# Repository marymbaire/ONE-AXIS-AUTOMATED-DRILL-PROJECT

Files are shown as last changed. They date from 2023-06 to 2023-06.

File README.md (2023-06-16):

# ONE AXIS AUTOMATED DRILL PROJECT
 All files regarding project will be saved here
Follow this link to install github desktop and clone the repository: https://youtu.be/xuq73UJrbwg
To add your files to github, create a branch and commit changes(add your files) to your branch, the owner( Mary) will merge changes to the main branch. Follow this link to create branch and commit changes to branch: https://youtu.be/Lf3DYRvCPFo. Your created branch should now be accessible on github desktop. Always push changes to your branch(not Main).

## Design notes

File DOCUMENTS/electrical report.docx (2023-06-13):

Electrical design

The design for the electrical circuit and simulation was done on Proteus because it was user friendly and suited our project needs.

Achievements

- Successfully controlled the feed rates and cutting speeds using feedbacks from the vibration, force and temperature sensor.
- Able to monitor the input and output parameters in real time using a Virtual Serial Monitor.
- Programmed our Arduino UNO microcontroller on Arduino software which would then control our process.

Challenges

- The virtual monitor delayed to display the data on the start of the simulation as the input parameters were altered.
- Running the stepper motor at higher speeds results to the motor wobbling.

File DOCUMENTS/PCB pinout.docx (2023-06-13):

| Signal pin | Power pin
Stepper | B7(pul),A8(dir) | N/a
L298N dc motor control | B12(EN),B13(IN1),B14(IN2) | N/A
Vibration sensor 1 | A5 | Pwr + gnd
Vibration sensor 2 | 10 | Pwr + gnd
Limit switch | A11 | Pwr + gnd
Encoder | B0, B1 | Pwr + gnd
Temperature sensor | B8, B9
Load cell | B4, B5
start | A3 | PWR
Stop | A1
Bluetooth module | B6, B7, B3 | Pwr + gnd
Start LED | A15
Stop LED

VIB+TEMP+LOAD = PWR+GND

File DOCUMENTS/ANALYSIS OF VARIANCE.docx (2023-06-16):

ANALYSIS OF VARIANCE(ANOVA)

1. Data collection

The goal of this analysis is to obtain optimal operating points for the stepper motor which provides linear feed to the dc motor station and the dc motor speed which provides rotary feed to the workpiece.

The two hypotheses in the experiment:

Null hypothesis: There is no significant difference in the mean quality of drilling across different levels of linear feed speed provided by the stepper motor and rotary speed determined by the DC motor.

Alternative hypothesis: There is a significant difference in the mean quality of drilling across different levels of linear feed speed provided by the stepper motor and rotary speed determined by the DC motor.

| Stepper Motor Speed (RPM) | DC Motor Speed (RPM) | Drill performance
E0 | 26.7 | 7958 | 0
E1 | 30.0 | 9422 | 0
E2 | 24.2 | 9422 | 0
E3 | 17.4 | 9604 | 3
E4 | 17.8 | 9775 | 3
E5 | 17.4 | 9712 | 2
E6 | 9.8 | 9778 | 8
E7 | 9.9 | 9671 | 5
E8 | 9.4 | 9733 | 8
E9 | 31.1 | 9785 | 5
E10 | 21.4 | 9836 | 5
E11 | 4.5 | 9706 | 3

2. ANOVA analysis

Drill performance extremes: 0- does not drill

10- drills efficiently

ANOVA: Two-Factor Without Replication
SUMMARY | Count | Sum | Average | Variance
E0 | 2 | 7984.7 | 3992.35 | 31452760
E1 | 2 | 9452 | 4726 | 44104832
E2 | 2 | 9446.2 | 4723.1 | 44159322
E3 | 2 | 9621.4 | 4810.7 | 45951450
E4 | 2 | 9792.8 | 4896.4 | 47601476
E5 | 2 | 9729.4 | 4864.7 | 46992635
E6 | 2 | 9787.8 | 4893.9 | 47708866
E7 | 2 | 9680.9 | 4840.45 | 46668427
E8 | 2 | 9742.4 | 4871.2 | 47274198
E9 | 2 | 9816.1 | 4908.05 | 47569283
E10 | 2 | 9857.4 | 4928.7 | 48163187
E11 | 2 | 9710.5 | 4855.25 | 47059551
Stepper Motor Speed (RPM) | 12 | 219.6 | 18.3 | 75.45818
DC Motor Speed (RPM) | 12 | 114402 | 9533.5 | 264111
ANOVA
Source of Variation | SS | df | MS | F | P-value | F crit
Stepper*DC Motor | 1434252 | 11 | 130386.5 | 0.974489 | 0.516708 | 2.81793
Stepper and DC Motor Separately | 5.43E+08 | 1 | 5.43E+08 | 4060.048 | 1.76E-15 | 4.844336
Error | 1471799 | 11 | 133799.9
Total | 5.46E+08 | 23
Total | 7.28E+08 | 35

3. Interpretation of ANOVA results
- The p-values indicate the significance of each factor and their interactions.
- Stepper Motor Speed has a p-value of <0.05, indicating that it has a significant effect on Optimal Drilling Performance.
- Drill Motor Speed also has a p-value of <0.05, suggesting a significant effect on Optimal Drilling Performance.
- Both the stepper motor speed and the drill motor speed independently significantly impact the quality or efficiency of the drilling process for PMMA material.
- The interaction between Stepper Motor Speed and Drill Motor Speed has a p-value of 0.516708, which is not statistically significant. Therefore, the interaction does not have a significant effect on Optimal Drilling Performance.
- The p- value of interaction between stepper motor speed and dc motor speed is greater than 0.5, thus we fail to reject null hypothesis; this means there is no significant difference in the mean quality of drilling across different levels of linear feed speed provided by the stepper motor and rotary speed determined by the DC motor. This means that the two variables can be controlled independent of each other to obtain best quality drilling.

From the analysis, the number of times the station is able to carry out a successful drilling operation is limited. The station exhibits a successful drilling operation when a starting hole is provided. Failure to drill can be attributed to the melting of PMMA and the sticking of the melted PMMA on the drill bit, making further drilling difficult. The new PMMA used melts when heated during heating. Using the current setup as it is, the optimal operating parameters is at 200 pulses/rev setting for stepper motor, where it operates at 21.6 rpm and for the dc motor, at 255PWM, which is equivalent to 9778rpm, which can be conditioned separately, with one of the variables held constant.

Recommendations

Using a geared dc motor for the drill station with operating speed limit of 300 rpm will provide sufficient torque to drill the PMMA as it melts. Temperature should also be control variable in the system due to thermal behavior of the PMMA strip.

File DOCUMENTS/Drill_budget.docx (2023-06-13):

ITEM | ADDRESS | UNITS | COST | TOTAL COST
Nema 17 Stepper motor | Nema 17 Stepper motor, 12V 0.4A, 1.8 degree, 2 phase 6 wires | ATO.com (https://www.ato.com/nema-17-stepper-motor-12v-0-4a-1-8-degree-2-phase-6-wires) | 1 | 6585/= | 6585/=
MLX90614ESF Non-contact Infrared Temperature Sensor Module (https://www.amazon.com/gp/slredirect/picassoRedirect.html?id=2962699365333126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) | Amazon.com : MLX90614 (https://www.amazon.com/MLX90614/s?k=MLX90614) | 1 | 1779/= | 1779/=
801S Vibration Sensor Module | 801S Vibration Sensor Module - ProtoSupplies (https://protosupplies.com/product/801s-vibration-sensor-module/) | 2 | 450/= | 900
HX711 LOAD CELL AMPLIFIER+5Kg | HX711 LOAD CELL AMPLIFIER+5Kg – Besomi Electronics (besomi-egypt.com) (https://besomi-egypt.com/products/hx711-load-cell-amplifier-5kg) | 1 | 2,310.27 | 2310.27
TB6600 DC 4A 9-42V Stepper Motor Driver | Generic TB6600 DC 4A 9-42V Stepper Motor Driver CNC @ Best Price Online | Jumia Kenya (https://www.jumia.co.ke/generic-tb6600-dc-4a-9-42v-stepper-motor-driver-cnc-61027590.html) | 1 | 5,395 | 5,395
L298N MOTOR DRIVER | Shop & Buy Online | Jumia Kenya (https://www.jumia.co.ke/catalog/?q=L298N+MOTO) | 1 | 1897 | 1897
12V DC MOTOR with drill chuck | Shop & Buy Online | Jumia Kenya (https://www.jumia.co.ke/catalog/?q=dc%20motor+chuck) | 1 | 300 | 2200
12v dc power supply | Shop & Buy Online | Jumia Kenya (https://www.jumia.co.ke/catalog/?q=12v+dc+power+supply) | | 3800 | 4000
total | | | | 25066

Automatic drill project budget

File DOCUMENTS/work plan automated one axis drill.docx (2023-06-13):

ONE AXIS AUTOMATED DRILL 10 WEEK WORK PLAN FOR OCTOBER- FEBRUARY SEMESTER

WEEK NUMBER | DATES | ACTIVITY | OBJECTIVE | INVOLLVEMENT
1. | 7th November- 13th November | In depth familiarization with existing model | - Analysis of mechanical set- up, identifying improvement areas. - Analysis of circuitry, identifying improvement areas - Analysis of used code and MATLAB files | 3 meetings during the week of all group members at the drill station (Monday, Wednesday, Friday)
2. | 14th November- 20th November | Full model design in SolidWorks | To design the full setup of the physical model with the improvements made. | Division of parts among group members, each tackling own design part, meetings to analyze progress and assemble, 2 group meetings.
3. | 21st November- 27th November | Importing CAD Files to MATLAB and modelling | Simulate the mechanical set-up in MATLAB | All group members involved. 3 meetings during the week.
4. | 28th November- 4th December | Finite element analysis in Abaqus | Analysis of forces of the system | All group members involved. 3 meetings during the week.
5. | 5th December- 11th December | Finite element analysis in Ansys | Analysis of forces of the system | All group members involved. 3 meetings during the week.
6 and 7 | 12th December- 23rd December | Circuit design in Proteus | Full circuit design of system | All group members involved. 2 meetings per week, total 4 meetings.
8 and 9 | 2nd January- 13th January | Programming of system and simulation | Development of embedded program. | All group members involved. 2 meetings per week.
10 | 14th January- 18th January | Analysis of objectives and challenges | | All group members involved. 2 meetings in the week.

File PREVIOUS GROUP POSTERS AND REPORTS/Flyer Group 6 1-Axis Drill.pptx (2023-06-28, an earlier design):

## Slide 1

Group members
1. Calvin Shibiriti.
2. Silvester Momanyi.
3. Allan Waithira.
4. Brilliant Chepkirui.
5. Joseph Kiarie.

OVERVIEW

STUDY AND DEVELOPMENT OF
AN AUTOMATED
1-AXIS DRILL

PROBLEM STATEMENT
Common problems in drilling include chatter vibrations, drill bit breakage, and work piece damage. This study seeks to use data from force, vibration, and temperature sensors to minimize chatter, and obtain quality cuts without increasing throughput time. Perspex was chosen for study since it resembles the human bone in properties.

OBJECTIVES
- Condition monitoring when drilling.
- Control the operation using STM32 Blue Pill.
- Conduct and validate Finite Element Analysis on Abaqus.

September 2022

Supervisor: Dr. Titus Mulembo

INTRODUCTION
Today’s market has simple drilling machines and often, human operator is required to drill the hole. Accuracy cannot be attained properly due to high temperatures which may spoil the job due to human errors. To overcome all these problems, this automated drilling machine is designed which is aimed to drill the holes automatically over a job according to the drilling depth data programmed through a key board.

JUSTIFICATION
There has been an increasing demand for acrylic materials such as PMMA, owing to their mechanical and thermal properties. In the medical industry, the drilling of bone is a common procedure in orthopaedic surgery to produce holes for screw insertion to fixate the fracture devices and implants. PMMA is compatible with the human bone which has promoted its use in orthopedic research.

EXPERIMENTAL WORK

Determination of drilling control parameters
Upload the program to the microcontroller
Run the experiment
Results and Data Collection
Evaluation and analysis

Sample Sensor Data

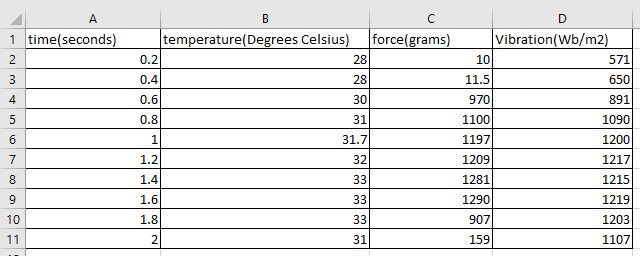
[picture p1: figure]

Fabricated Drill Set Up

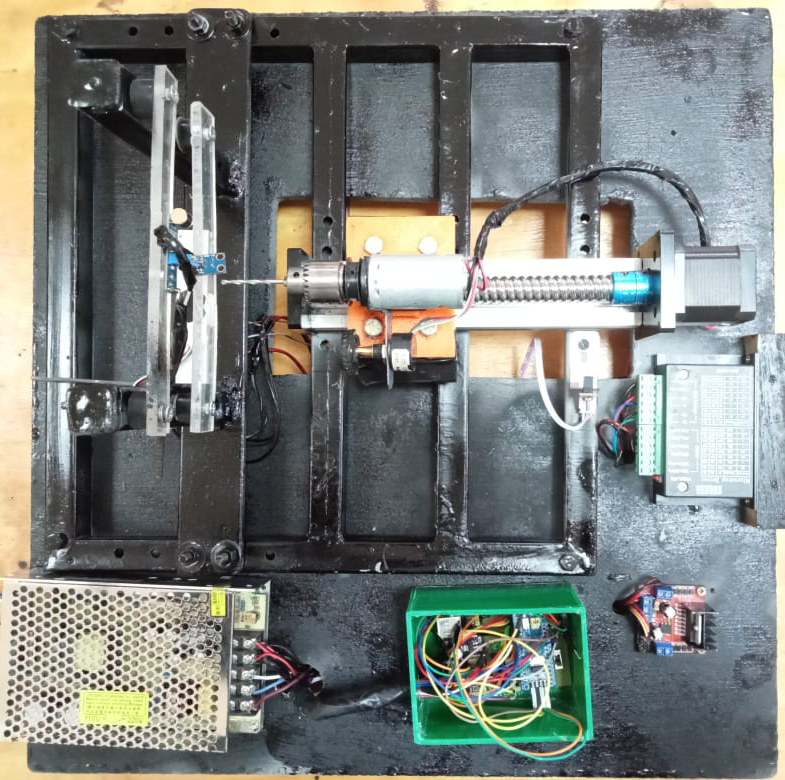
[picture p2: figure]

VARIABLES

- Feed rate
- Spindle speed
- Drill bit diameter
- Hole Depth

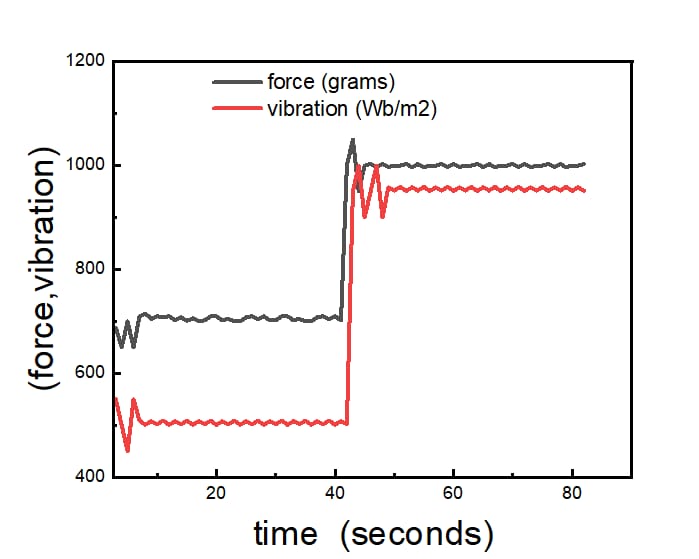
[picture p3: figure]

Graph of vibration (Wb/m²) against time (seconds)

RESULTS

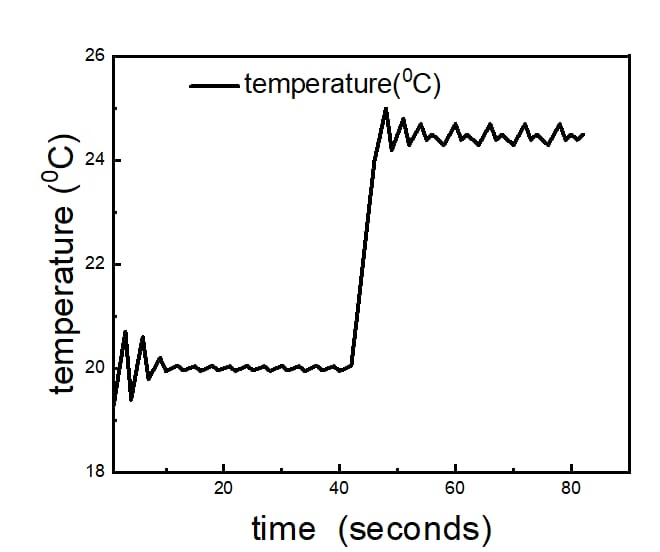
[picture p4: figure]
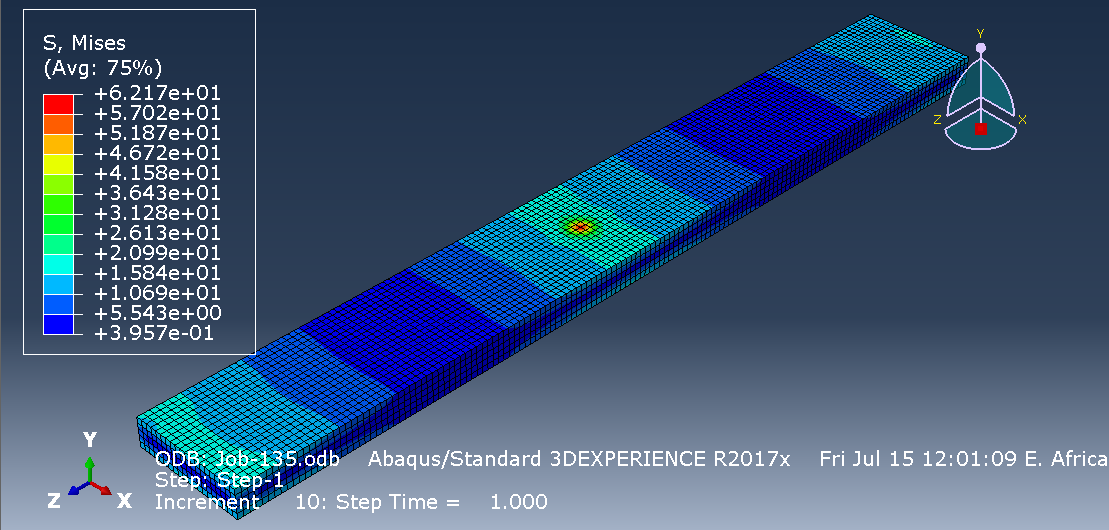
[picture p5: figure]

Analysis of PMMA when subjected to a load

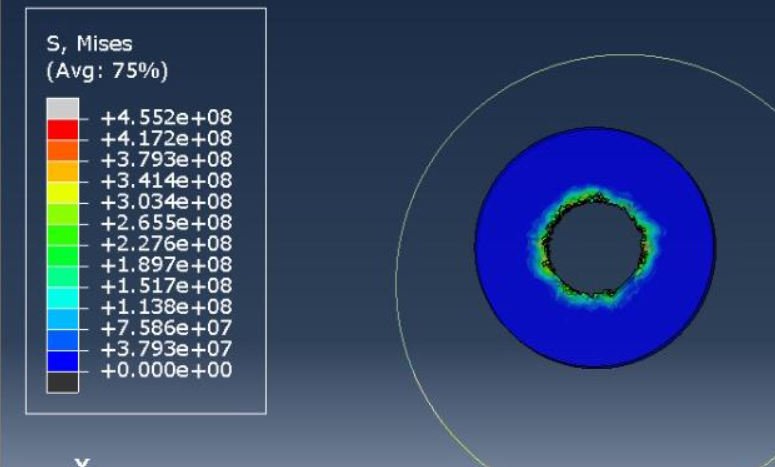
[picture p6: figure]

Temperature evolution upon drilling

- The condition of the drilling action was monitored using the three sensors; temperature, force, and vibration sensors.
- Data was collected and transmitted to an external computer module via Bluetooth.
- The data was simulated and analyzed using Matlab.

Graph of Temperature (Degrees Celsius) against Time (seconds)

CONCLUSION

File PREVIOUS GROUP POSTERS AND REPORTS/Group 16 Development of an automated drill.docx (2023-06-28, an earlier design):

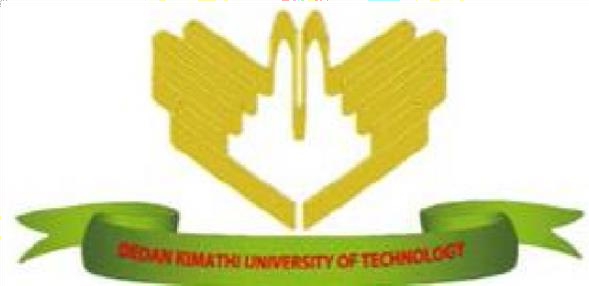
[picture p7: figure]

DEDAN KIMATHI UNIVERSITY OF TECHNOLOGY

SCHOOL OF ENGINEERING

DEPARTMENT OF MECHATRONICS ENGINEERING

1. ONYUNA AGGREY OMONDI E022-01-0747/2017
2. NAFULA FAITH E022-01-0749/2017
3. ADEGU GLORIA VUHYA E022-01-0737/2017
4. ISAAC MWONDI VENANT E022-01-0726/2017

TITLE: STUDY AND DEVELOPMENT OF AN AUTOMATED DRILL

A project proposal submitted in partial fulfillment of the requirement for the award of the Degree of Bachelor of science in Mechatronic Engineering in the Dedan Kimathi University of Technology.

FEBRUARY 2022

# ACKNOWLEDGEMENT

We would like to thank the almighty God for gift of life and good health during the preparation of this research undertaking. Our heartfelt gratitude also goes to our able supervisor Dr. Titus Mulembo, who we have worked closely with in preparation and undertaking of this research. We also wish to acknowledge the entire Department of Mechatronic Engineering of Dedan Kimathi University of Technology for the support they have given us during this process. To our colleagues, friends and parents who gave us support in any manner, we are grateful indeed.

ABSTRACT

Acrylic polymers and co-polymers are currently widely used in industry in all kinds of applications due to their chemical purity, stability, high heat resistance, sunlight resistance, excellent weathering, low-temperature performance, water resistance, and hydrophobicity. Acrylic is very scratch resistant compared to other transparent plastics. It is a lighter alternative to glass and an

economical substitute for polycarbonate in applications where strength is not crucial.

Due to its wide applications, various manufacturing processes are performed on acrylic, drilling one of them. Drilled holes can be produced on the acrylic using conventional or non-conventional drilling processes. Conventional micro-drilling uses drill bits of different configurations such as twist, spade, D-shaped, single flute, compound drill, and coated micro drill. In contrast, non-conventional micro-drilling involves electrical, chemical, mechanical, and thermal means, including laser, EDM, ECM, SACE, electron beam, ultrasonic vibration, or combinations of these approaches.

Various researchers and manufacturing companies working with PMMA have proposed different guidelines for drilling PMMA. The spindle speed, feed rate, tool point angle, coolant & lubricating agent, vibration, tool material, clearance, and chip length influences the drilling process. These machining parameters must be optimized in order to produce quality holes and maintain the material properties of the machined workpiece for long service life

The current work focuses on developing an automated drilling machine that measures the drilling parameters required for drilling different hole sizes on PMMA.

© 2017 The Authors. Published by Elsevier B.V.

Peer-review under responsibility of the scientific committee of The 50th CIRP Conference on Manufacturing Systems.

## 1. INTRODUCTION

PROBLEM STATEMENT

Current automatic CNC machines used to drill PMMA are expensive. In addition, the alternatives used, such as the hand drill, are frequently marred by drill bit breakage, mainly inexperienced users. On the other hand, if the workpiece or drill-bit is not tightly held, walking phenomena occur where the drill bit tends to skid away from the desired drilling coordinates giving a significant blow to the precision of drilled holes.

There is a need to develop an inexpensive automated drilling machine that addresses all these challenges. In contrast with the available CNC drilling machines, the proposed automated drill has the advantages of lower cost, less construction difficulty, and maintenance that is more convenient. It is also a more straightforward use; hence, it produces quality and curbing bit breakage for thin drill bits and drill bit wear for thick drill bits.

JUSTIFICATION

Currently, the drilling of PMMA is by using automatic CNC machines. However, this method has proved to be expensive, and its availability to the ordinary person is limited.

The other alternative used is the hand drill frequently marred by the drill bit breakage, primarily inexperienced users. On the other hand, if the workpiece or drill bit is not tightly held, a walking phenomenon occurs where the drill bit tends to skid away from the desired drilling coordinates giving a significant blow to the precision of the drilled holes.

The automated drill finds it suitable for PMMA drilling because it is less expensive. Therefore, it saves on costs has high accuracy and precision. In addition, this production of quality drill holes and the machining parameters are continuously monitored and optimized for the entirety of the drilling process, thus saving time.

In contrast with the available CNC drilling machines, the proposed automated drill will have the advantages of lower costs, less construction difficulty, more convenient maintenance, and simpler to use, hence producing quality and curbing bit breakage for thin drill bit wear for thick drill bits.

In the recent past, we have seen a tremendous rise in the use and application of acrylic polymers. From the aerospace industry to the entertainment industry, PMMA is being used for various purposes, leading to various manufacturing processes, including drilling.

The automated drill finds its suitability in PMMA drilling because it is less expensive has high accuracy and precision. The machining parameters are automatically monitored and optimized for the entirety of the drilling process. In addition, the machine uses the peck cycle drilling, where the workpiece is drilled intermittently, for adequacy.

## OBJECTIVES.

### Main Objective.

To design and fabricate an automated drilling machine for PMMA drilling.

Specific Objectives

## i. To design and fabricate an automated drilling machine.

## ii. To design mechanical assembly simulations using CAD software.

## iii. To design an electrical circuit that interfaces with the sensors during the drilling operation.

## iv. To monitor force, thermal fluctuations, and optical characterization

## v. To enable drilling of quality, thin/long holes.

## vi. To design optimal machining conditions for drilling of PMMA (polymethyl methacrylate).

## PROJECT SCOPE

As outlined above, our project will mainly focus on designing and fabricating an automated drill that ensures drilling of quality thin, long holes while monitoring parameters such as temperature and vibrations to determine optimum drilling parameters.

2. METHODS

In order to achieve quality drilling of holes using optimum conditions such as the feed rate, drilling speed, and drill bit diameter, we had to follow the required steps as follows:

a) Coming up with CAD Models and electrical circuits using softwares: achieved through Solidworks, Proteus, Fritzing
b) Simulations of the whole system and its components using Simscape, Proteus, Abaqus: Simulations that show how the system would move prior to fabrication, temperature and force simulations of the workpiece and simulations of the electric components too.
c) Actual fabrication of the rig: Assembly of all the mechanical parts. Processes included welding, woodcutting, bolting, painting
d) Circuit interfacing of the sensors, actuators and drivers and their programming:
e) Running the experiments and data collection and observation to determine the optimum parameters: Running the motors sequentially to approach the workpiece, drill the PMMA while sensors are collecting data then move back to the original position.

Experimental Rig

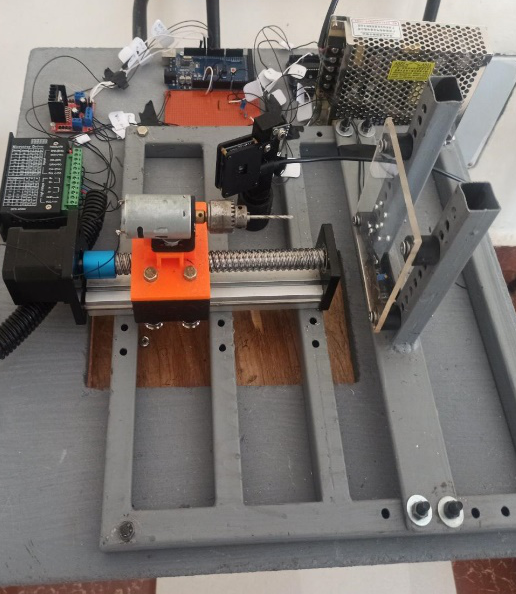
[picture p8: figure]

Figure 1: an image of the whole assembly

Components

- NEMA 17 Stepper motor.
- DC Motor.
- 801S Vibration sensor module.
- MLX0614 non-contact Infrared temperature sensor.
- TB6600 Microstep stepper motor driver.
- L298N DC motor driver.
- Arduino Mega

Procedure

This involved drilling with drill bits of different diameters while varying their feed rates until the optimum parameters were identified.

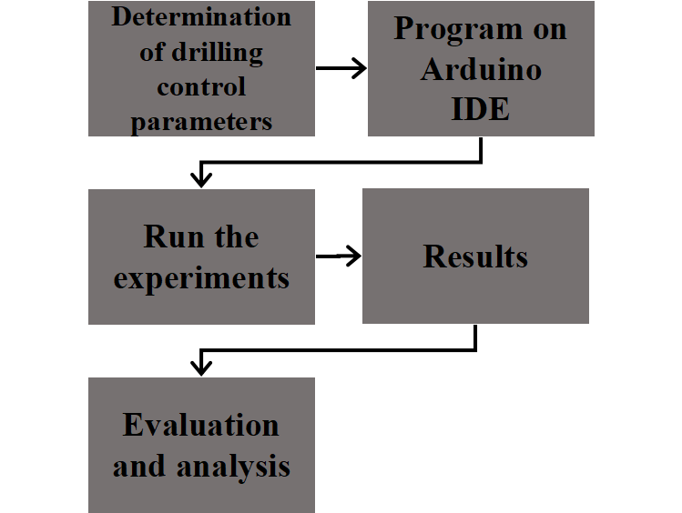
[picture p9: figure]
FLOW CHART

3. EXPERIMENTAL RESULTS

Temperature from MLX90614

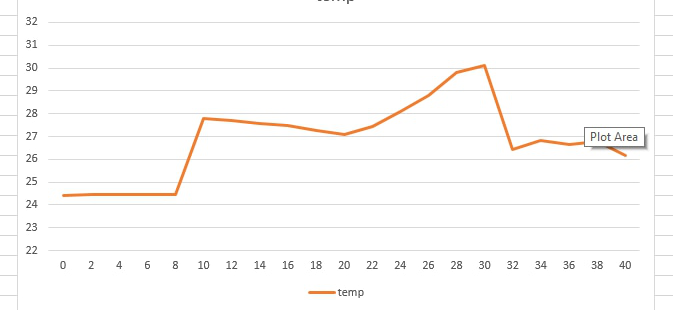
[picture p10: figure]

Figure 2: A graph of temperature from MLX90614 temp sensor

Temperature from ABAQUS simulation

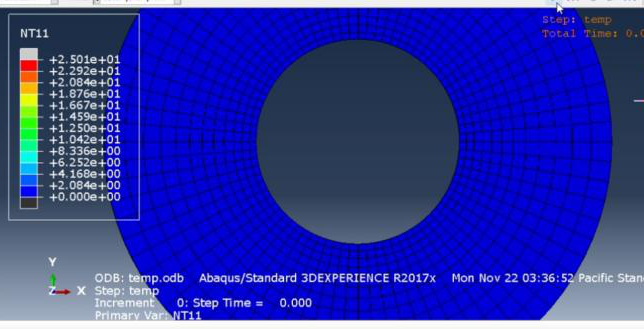
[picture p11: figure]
WhatsApp Image 2022-02-16 at 12.07.23

Figure 3: An Image of the temperature simulation using Abaqus before the drilling process starts

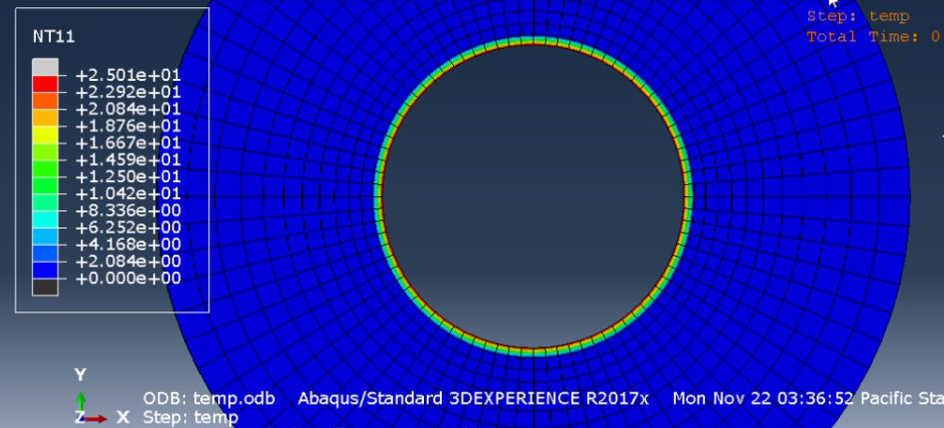
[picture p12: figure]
WhatsApp Image 2022-02-16 at 12.07.26

Figure 4: An image of the workpiece in Abaqus temperature simulation during the drilling process

Expected Vibration output from 801S Vibration sensor

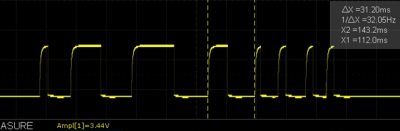
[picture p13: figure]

Figure 5: 801S Vibration sensor expected output

Its output switches shortly from LOW to HIGH depending on the vibrations during the drilling process. A threshold value was set on the onboard potentiometer where drilling was safe.

Hole Quality

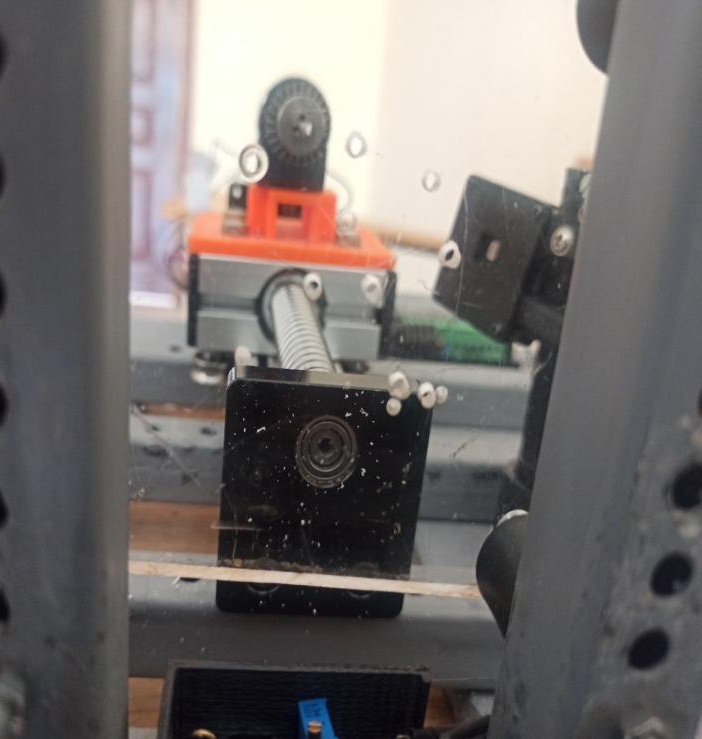
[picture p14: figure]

Figure 6: An Image of the PMMA Workpiece showing different holes

4. DISCUSSION

The drilling speeds were achieved with (Pulse Width Modulation) PWM by the Arduino Mega 2560. The motor had a maximum (Revolutions per Minute) RPM of 12000, which in turn, correlated which a maximum setting of 255 on PWM. We used different RPM according to the drill bit diameter in order to ensure we achieved quality holes.

We also had another parameter to control which was the feed rate (mm/rev). This is the velocity at which the cutter is advanced against the workpiece. This was being controlled by the stepper motor.

The following are the drilling parameters that were achieved to produce quality holes on the PMMA sheet.

During the drilling process, we were monitoring vibrations and temperature to ensure optimal parameters that would lead to quality holes. The temperature was being monitored by the MLX 90614 temperature sensor while the vibrations were being monitored by the 801S vibration sensor.

Temperature from Abaqus simulations matched with the actual results from the experiment as predicted.

5. CONCLUSIONS
- The automated drill was able to drill as expected, and the parameters for optimum drilling were determined for production of quality holes.
- Temperature and vibration were able to be monitored during the drilling process.
- The vibration signals are considered to contain reliable features for monitoring drill wear and breakage.
- It is also time effective, inexpensive and easy to use.

RECOMMENDATIONS

We would recommend that if the project is to be improved, there should be:

- An introduction to feedback control
- Making the project smart such as use of a Bluetooth module to operate it from a remote position.
- Introducing another axis.

REFERENCES

1) Brandrup J, Immergut EH, Grulke EA, editors. Polymer Handbook. 4th ed. New York: John Wiley & Sons; 1999
2) Ulrich H. Introduction to Industrial Polymers. Munich: Hanser; 1982
3) Rey-Vinolas S, Engel E, Mateos- Timoneda MA. Polymers for bone repair. In: Bone Repair Biomaterials. Woodhead Publishing Series in Biomaterials. UK: an imprint of Elsevier; 2019. pp. 179-197. DOI: 10.1016/ b978-0-08-102451-5.00007-x
4) Modelling and optimization of temperature in orthopaedic drilling: An in vitro study RUPESH KUMAR PANDEY, SUDHANSHU SEKHAR PANDA
5) https://www.researchgate.net/publication/232167295_Finite-Element_Analysis_of_Forces_in_Drilling_of_Ti-Alloys_at_Elevated_Temperature
6) Finite Element Analysis of Drilling Frame on Down-the-Hole Drill Based on Mechanical Mechanics and Mechanical Properties | Scientific.Net : https://www.scientific.net/AMR.908.282
7) (PDF) 3D Finite Element Modelling of Drilling Process: https://www.researchgate.net/publication/317271692_FEM_Simulation_of_Tool_Wear_in_Drilling

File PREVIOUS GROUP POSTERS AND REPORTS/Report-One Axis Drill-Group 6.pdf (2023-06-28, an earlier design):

### P a g e | 1

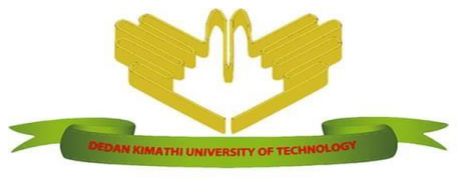
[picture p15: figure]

DEDAN KIMATHI UNIVERSITY OF TECHNOLOGY

MECHATRONIC DEPARTMENT – SCHOOL OF ENGINEERING

1. SHIBIRIT CALVINE | E022-01-1056/2018
2. OMWAGA SILVESTER | E022-01-1412/2018
3. WAITHIRA ALLAN | E022-01-0496/2018
4. CHEPKIRUI BRILLIANT | E022-01-1053/2018
5. KIARIE JOSEPH | E022-01-1085/2018

TITLE: STUDY AND DEVELOPMENT OF AN AUTOMATED DRILL

STUDENTS` REPORT

Submitted in September 2022

A report submitted in partial fulfilment of the requirements for the award of a degree in

Mechatronic Engineering.

### Department of Mechatronic Engineering

ABSTRACT

There are broad applications of high aspect

ratios, high quality holes. However, it is very

difficult for conventional drilling methods to

obtain deep holes, especially with high aspect

ratio, while keeping vibrations, forces, and

thermal evolution on check. This automated 1-

axis drill provide a promising solution for

efficient drilling of deep holes with high-

precision material removal, reduced cracks or

breakage of workpiece, minimized heat-affected

zones. Monitoring the system is crucial in

determining optimal drilling parameter which

can in turn be used in a system control. On the

same note, this research analyzes the behavior

of PMMA during the drilling action. Finally,

the analysis of the material composition could

help other students or researchers in studying

plastics behaviour to heat and stress.

Key Words: Automatic 1-Axis Drill,

PMMA, force, vibrations, temperature

### 1. Introduction

Drilling is a cutting process that uses a drill

bit to cut a hole of circular cross-section in solid

materials. Recently, drilling of quality holes in

Perspex has gained a lot of research interest

especially in thermoplastics and human bones.

This study attempts to contribute to this

endeavor by proposing to design and fabricate a

1-axis automated drilling machine that will

monitor key conditions of the system during operation. To achieve quality drilling, the

effects of three sensors will be studied for:

drilling | force, | vibration, | and | cutting
temperatures | monitoring. | The | automated

drilling machine and its electronics are designed

in CAD and simulated in Matlab. Temperature

evolution and stresses on the Perspex are

studied using FEA. The collected data in a live

feed and simulations done for analysis.

Mechanical transmission is done with a stepper

motor based on the drilling depth fed into the

program. | The | entire | process | utilizes

mechatronics and various related fields in order

to fulfil the drilling objective.

### 1.1 Problem Statement

Common problems in drilling include chatter

vibrations, drill bit breakage, and workpiece

damage. This can present challenges in

precision drilling applications in the delicate

technological drilling and medical industry.

This study seeks to use data from force,

vibration, and temperature sensors to minimize

chatter, and obtain quality cuts without

increasing throughput time. Perspex was

chosen for study since it resembles the human

bone properties.

### 1.2 Justification

In the medical industry, the drilling of bone is a

common procedure in orthopedic surgery to

produce holes for screw insertion to fixate the

fracture devices and implants. It also helps with

fix plates and screws that fastens broken body

parts for immobilization. In the recent past,

bone drilling has gained popularity following its importance in reduction of tissue damage, a

process known as osteonecrosis. PMMA has

similar properties to the bone hence this study

can be used in orthopedic drilling research.

### 2. OBJECTIVES

2.1 Main Objective

To design and create a 1-axis automatic drilling

machine with a monitoring system of the

drilling parameters.

2.2 Other Objectives

- To design mechanical
assembly simulations using CAD.
- To program the sensos and actuators for the operation using STM32 Blue Pill.
- To monitor the drilling
operation in MATLAB.
- To conduct a Finite Element Analysis on Abaqus.

### 2.3 Project Scope

Interfacing of all software necessary for the

design of the automated one axis drilling

machine are bound within the scope of this

project. In addition, assembling of the hardware

components and whole design architecture also

falls under the scope of the project. Finally,

some of the properties deemed important and

worth evaluating from this project include its

efficiency and reliability. Designing of the

proposed automated one axis drilling machine

is covered in the scope of this project.

3. METHOD

### 3.1 Steps

In order to achieve quality drilling of holes

using optimum conditions such as the feed

rate, drilling speed, and drill bit diameter,

we had to follow the required steps as

follows:

a) Coming up with CAD Models and electrical

circuits using software: achieved through

Solidworks, Proteus, Fritzing.

b) Simulations of the whole system and its
components | using | Simscape, | Proteus,

Abaqus and Solidworks:

- Simulations that show how the system would

move prior to fabrication,

i. temperature and force simulations of the

work piece

ii. Simulations of the electric components.

iii. Mechanical design simulation.

c) Actual fabrication of the rig:
- 3D printing of components such us:
i. pulleys,

ii. electrical cabinet.

- Assembly of all the mechanical parts.

Processes included:

i. welding,

ii. bolting,

iii. painting

d) Circuit interfacing of the sensors, actuators

and drivers and their programming:

e) PCB fabrication.
f) Running the experiments and data collection

and observation to determine the optimum

parameters: Running the motors sequentially

to approach the workpiece, drill the PMMA

while sensors are collecting data then move

back to the original position.

g) Interfacing the digital twin of model.

### 3.2 Components

- NEMA 17 Stepper motor.
- DC Motor.
- 801S Vibration sensor module.
- MLX0614 | non-contact | Infrared

temperature sensor.

- TB6600 Micro-step stepper motor

driver.

- L298N DC motor driver.
- STM32 Blue Pill microcontroller.
- Speed Encoder
- Photoelectric Limit Switch
- Ball screw

### 3.3 PROCEDURE

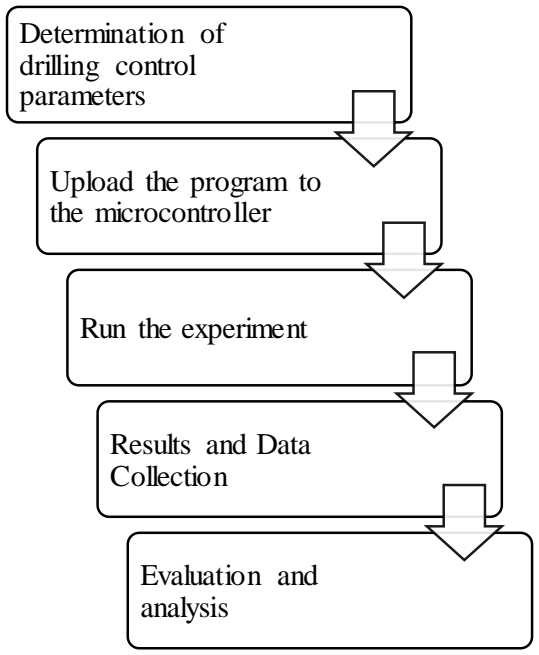
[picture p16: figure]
Determination of drilling control parameters; Upload the program to the microcontroller; Run the experiment; Results and Data Collection; Evaluation and analysis

### 3.4 Components

Stepper Motor

One of the main electrical components used

in this project is the stepper motor. It

contains the carriage that holds the DC motor

in | position.

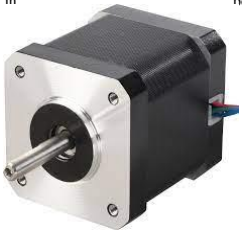
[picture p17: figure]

Figure 1: A stepper motor

In a stepper motor, the electromagnets are

energized by an external control circuit, such

as a microcontroller. To make the motor

shaft turn, first one electromagnet is given

power, which makes the gear's teeth

magnetically attracted to the electromagnet's

teeth. When the gear's teeth are thus aligned

to the first electromagnet, they are slightly

offset from the next electromagnet. So, when

the next electromagnet is turned on and the

first is turned off, the gear rotates slightly to

align with the next one, and from there the

process is repeated. Each of those slight

rotations is called a "step," with an integer

number of steps making a full rotation. In

that way, the motor can be turned by a

precise angle. Stepper motors are ideally

suited for precise positioning of an object or

precise control of speed without having to

resort to closed loop feedback. These motors

rotate in step-wise i.e., this stepper motor

rotates a precise angular distance, one step

for each pulse that is delivered to its drive circuit. The motor used in this project work

has a step angle of 1.80 per pulse. In order to

rotate the motor shaft for one complete

revolution i.e., 3600, it is required to supply

200 pulses (360 / 1.80 = 200) to the motor’s

drive circuit. This drive circuit is then

connected to drilling machine, which is the

main device of the project.

STM 32 Blue Pill

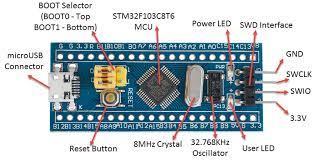
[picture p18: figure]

Figure 2: STM 32 Blue Pill

A | STM32 | is | a | high-performance

development board used as a microcontroller

in this experiment. It has a range of I/O

peripherals with multiple communication

interfaces such as 12C, SPI, and USB.

STM32 was used in this experiment as it is

cheap, board-friendly, and has a lot of

features required for this project.

Photoelectric Limit Switch

A limit switch is integrated in the structure

to help to help identify the absolute home

position and prevent the stepper motor from

damage. This switch is integrated in the

microcontroller as an input signal. Whenever

the limit switch is activated, active low

signal will be generated, based on this signal

the microcontroller can recognize the

position of drill motor. Thus, the power can

be saved to a maximum extent.

### 4. RESULTS

After the experiment, data from the three

sensors was collected. The data was

transferred through a live feed to an

external computer module and analyzed.

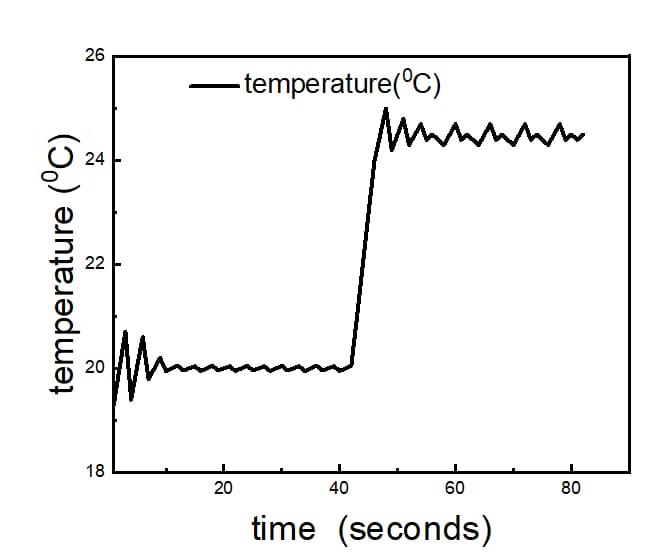
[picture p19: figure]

Figure 3: Temperature measured against time

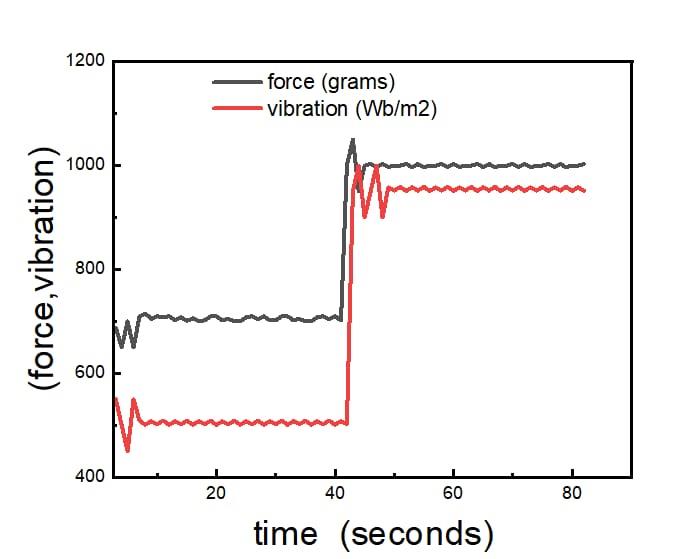
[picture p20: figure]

Figure 4: Force and Vibrations against time

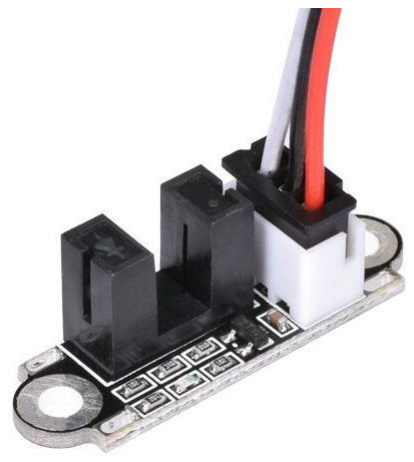
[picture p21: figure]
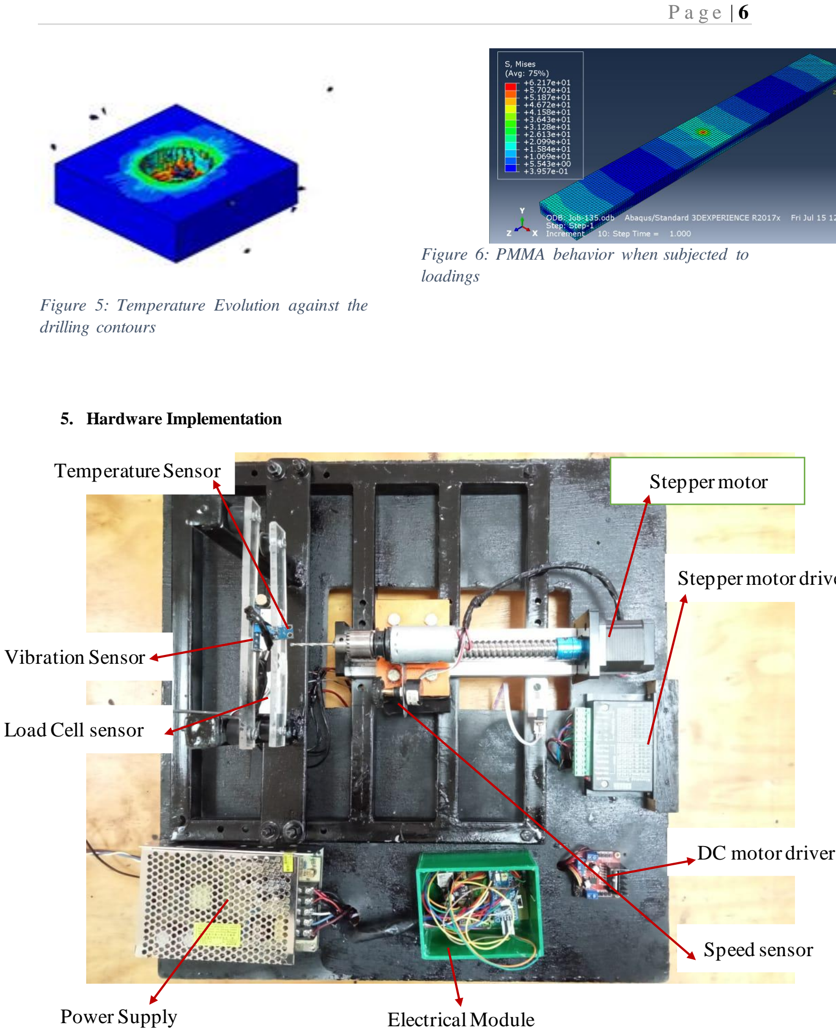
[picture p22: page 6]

Figure 5: Temperature Evolution against the drilling contours

Figure 6: PMMA behavior when subjected to loadings

### 5. Hardware Implementation

### Temperature Sensor

### Vibration Sensor

### Stepper motor

### Stepper motor driver

### DC motor driver

Power Supply | Electrical Module

### Load Cell sensor

### Speed sensor

### 6. CONCLUSION

In this experiment, a 1-axis drill was designed

and fabricated as expected. Automation was

achieved through efficient programming in

STM32 Blue pin. The condition of the drilling

action was monitored using the; temperature,

force, and vibration sensors. The depth of the

holes was determined by the program. The

results measured were used as reference data for

prospective study.

REFERENCES

[1] Madekar, K. J., Nanaware, (2016).

Automatic mini-CNC machine for

| PCB | | drawing | and

drilling. (IRJET), 3(02), 1107-1108.

[2] Sanjaya, G., 2005, Automatic
Drilling | | Machine | with | 89C51.

Undergraduate final project no.

02010741/ELK/2005

[3] Khan, M. N., Ansari (2022).

Fabrication and Automation of Drilling

Machine by Using Arduino. Vol. 1224,

No. | 1, | p. | 012007). | IOP

Publishing.

[4] Niranjan, G., Chandini, P. (2013).

Automated drilling machine with depth

controllability. IJSEA. 2(4), 90-93.

[5] Guangqing, N. (2017). Application

of automatic control technology of

drilling machine based on PLC. Acta

Technica Csav, 62(1), 530

Acknowledgement

To begin with, we would like to thank the Almighty God for his love and unending grace. He has been

the guiding light to us throughout our work.

Secondly, our most profound gratitude goes to supervisor Dr. Titus Mulembo, who greatly helped in

the realization of this project from conception to completion. His guidance and insights have been

fundamental in this project.

We would also like to pass our gratitude to Mechatronics Lab led by Mr. Kibe and Ms. Consolata for

the support they have given us during this process. Finally, we wish to thank our peers, colleagues,

friends, and parents for their invaluable help.

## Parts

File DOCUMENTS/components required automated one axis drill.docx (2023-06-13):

Design and fabrication of a 1 axis drilling machine for quality drilling of PMMA

No | ITEM | DETAILS | UNITS | COST | TOTAL COST
1. | WIT MOTION VIBRATION SENSOR | WT 90ICL AHRS IMU CONNECTIVITY: TYPE C, BLUETOOTH 2.0 INPUT VOLTAGE: 5V CURRENT: <40 mA | 1 | 12,000 | 12,000
2. | GEARED 12V DC MOTOR WITH ENCODER | UXCELL GEAR MOTOR GEAR RATIO: 9:28:1 463 RPM | 1 | 2500 | 2.,500
3. | LOAD CELL WEIGHT SENSOR | HX711 5KG WEIGHT LIMIT | 1 | 4500 | 4500
4. | RASPBERRY PI B4 MICROCONTROLLER | MODEL SC15184 PI4 MODEL B 5V, 3A | 1 | 17,000 | 17,000
5. | PMMA | | | | 8,000
6. | DISPLACEMENT ULTRASONIC SENSOR | HC SR04 5V,15Ma Measuring distance: 2cm-450 cm | 2 | 500 | 1000
| TOTAL | | | | 45,000

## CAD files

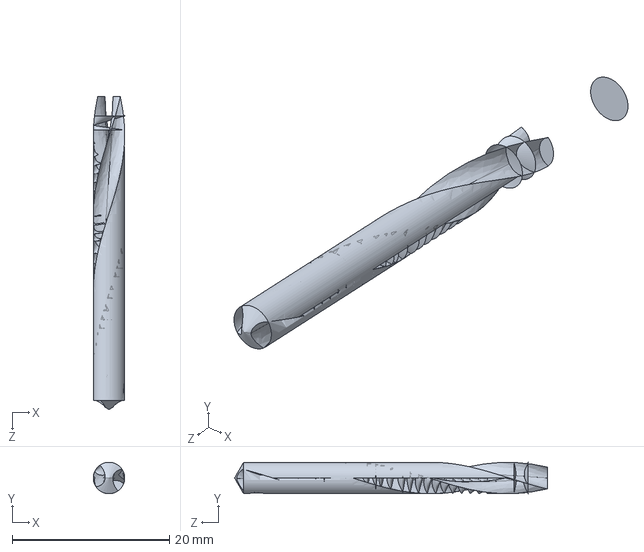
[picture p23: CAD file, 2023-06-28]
Allan/ansys/New drill bit.IGS
4.00 x 4.00 x 50.0 mm

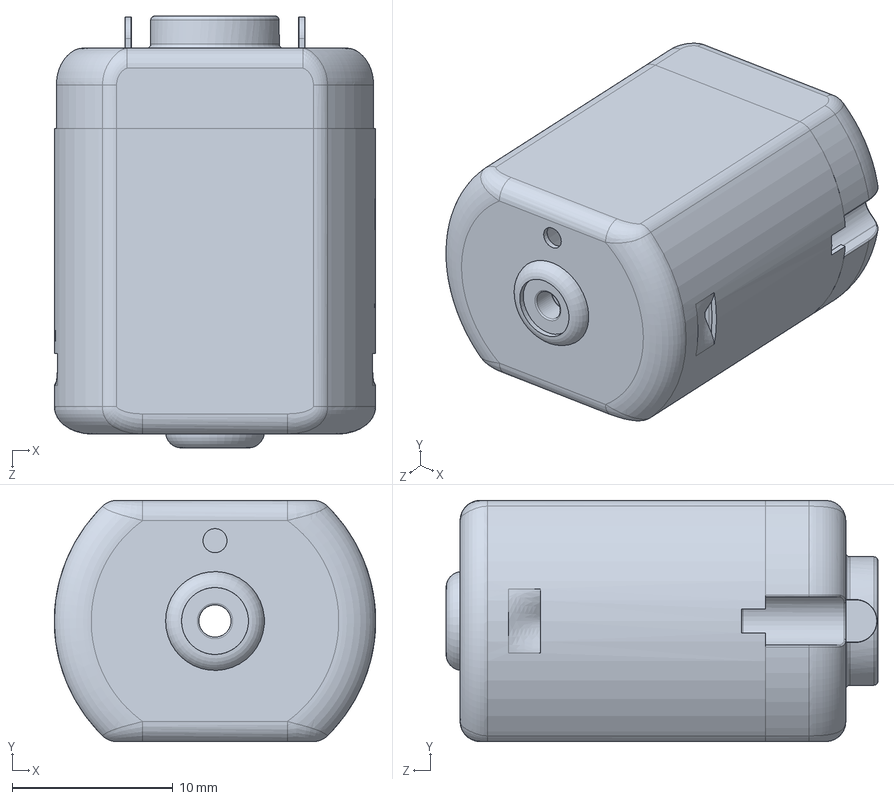
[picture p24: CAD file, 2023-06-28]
Allan/matlab/Dc motor/cassing.SLDPRT
20.0 x 15.0 x 26.9 mm

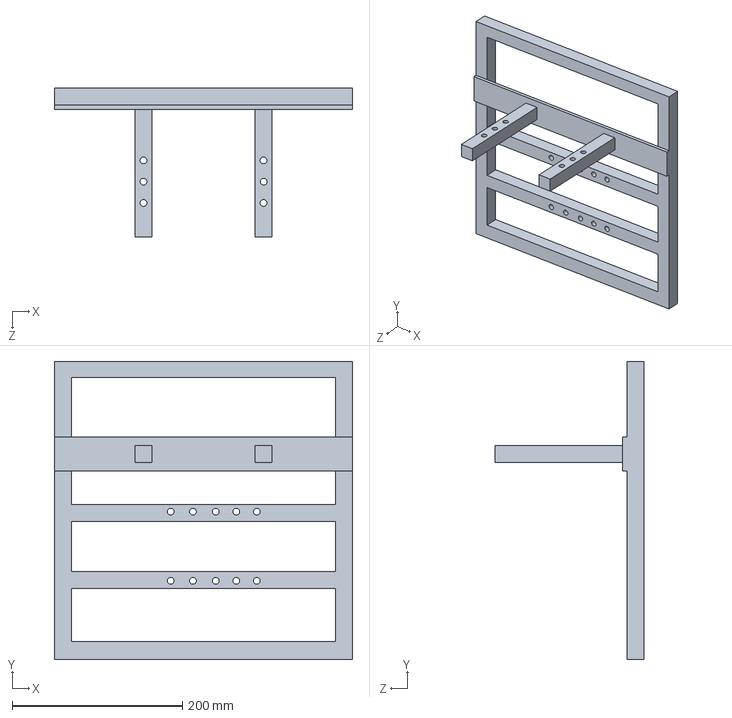
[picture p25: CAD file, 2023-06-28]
Allan/One axis drill project/base .1.SLDPRT
350.0 x 350.0 x 175.0 mm

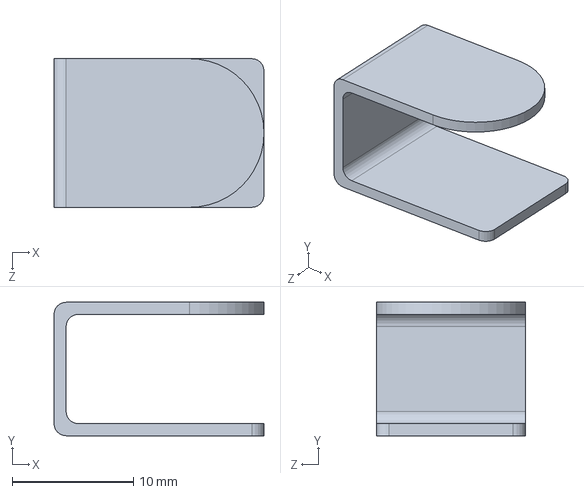
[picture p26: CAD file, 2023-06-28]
Allan/One axis drill project/Dc motor/dc motor support.SLDPRT
17.3 x 11.0 x 12.2 mm

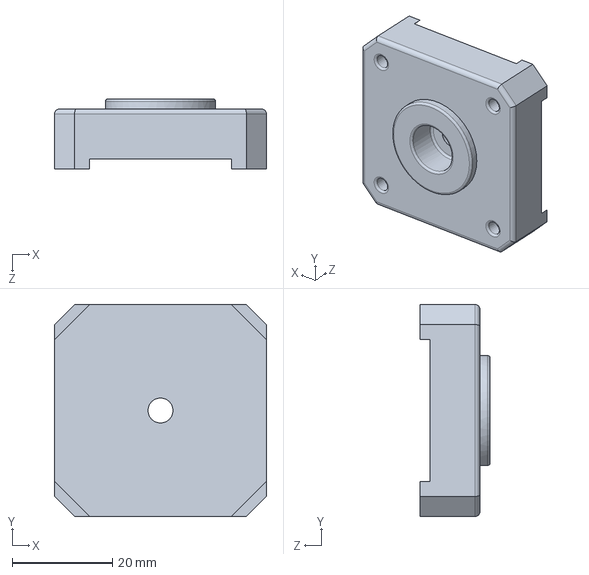
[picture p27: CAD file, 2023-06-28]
Allan/One axis drill project/Stepper motor/Base Plate.SLDPRT
42.3 x 42.3 x 14.0 mm

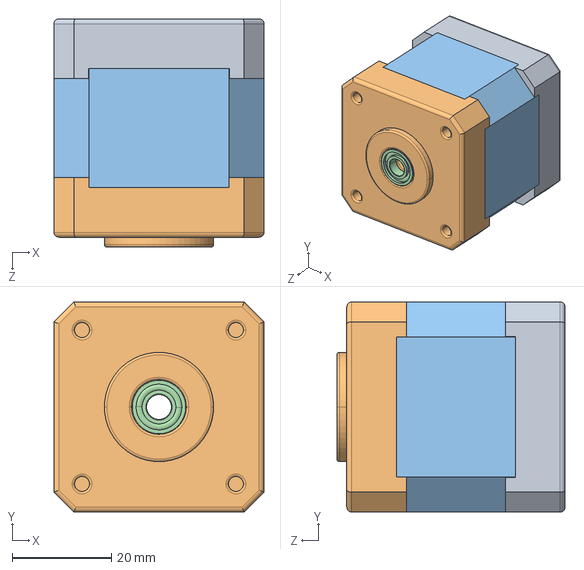
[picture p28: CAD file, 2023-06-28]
Allan/matlab/Stepper motor/case_Default_sldprt.STEP
42.3 x 42.3 x 46.0 mm

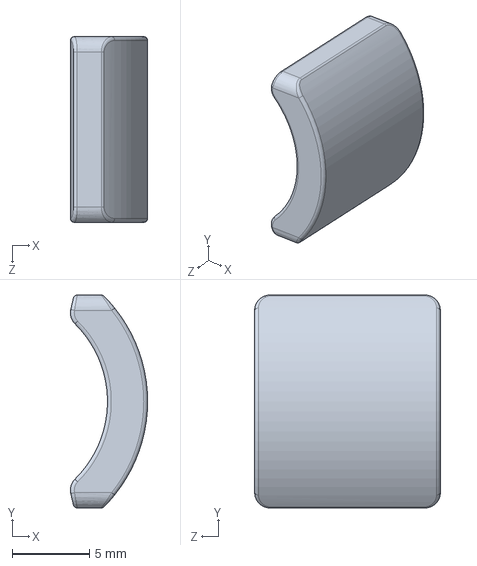
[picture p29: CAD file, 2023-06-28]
Allan/One axis drill project/Dc motor/Part3 motor.SLDPRT
4.99 x 13.8 x 12.0 mm

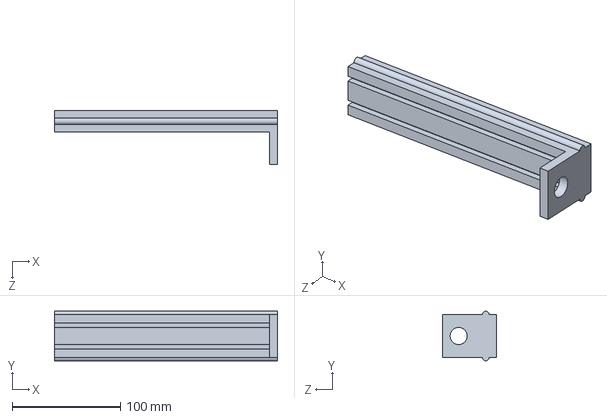
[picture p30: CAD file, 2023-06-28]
Allan/One axis drill project/Part3.SLDPRT
206.0 x 46.0 x 50.0 mm

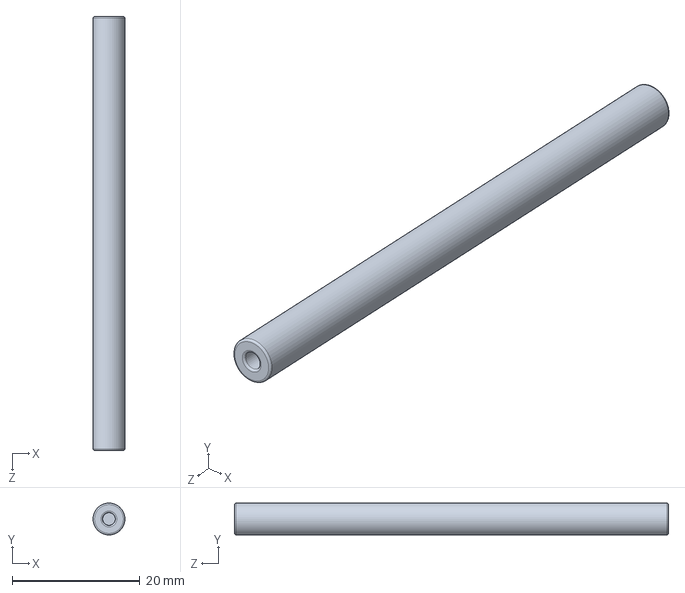
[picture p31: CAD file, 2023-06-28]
Allan/One axis drill project/Stepper motor/Axial Rod.SLDPRT
4.99 x 5.00 x 68.0 mm

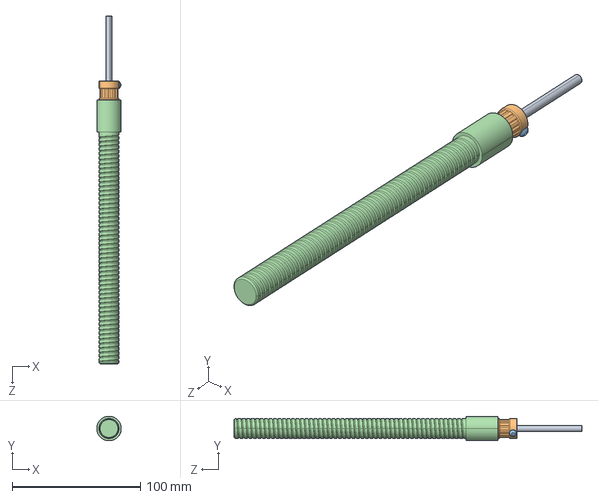
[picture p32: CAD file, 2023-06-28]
Allan/matlab/Stepper motor/rotary part_Default_sldprt.STEP
19.1 x 19.1 x 271.6 mm

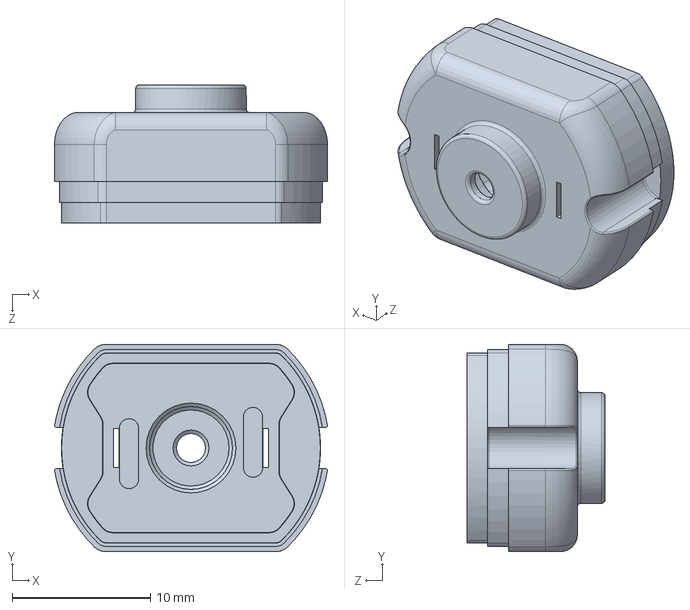
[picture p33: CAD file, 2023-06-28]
Allan/One axis drill project/Dc motor/Part1 motor.SLDPRT
19.7 x 15.0 x 10.0 mm

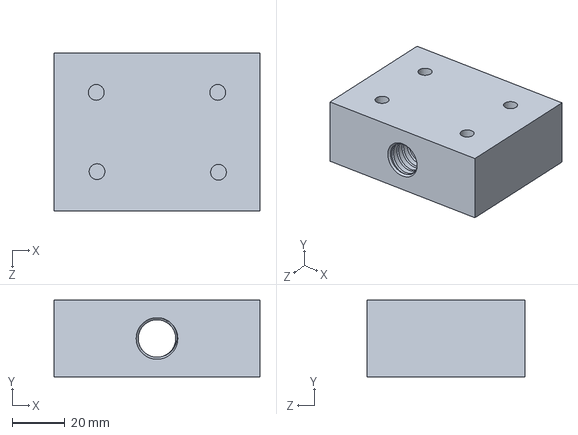
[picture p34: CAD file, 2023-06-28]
Allan/One axis drill project/Part1.SLDPRT
78.0 x 29.0 x 60.0 mm

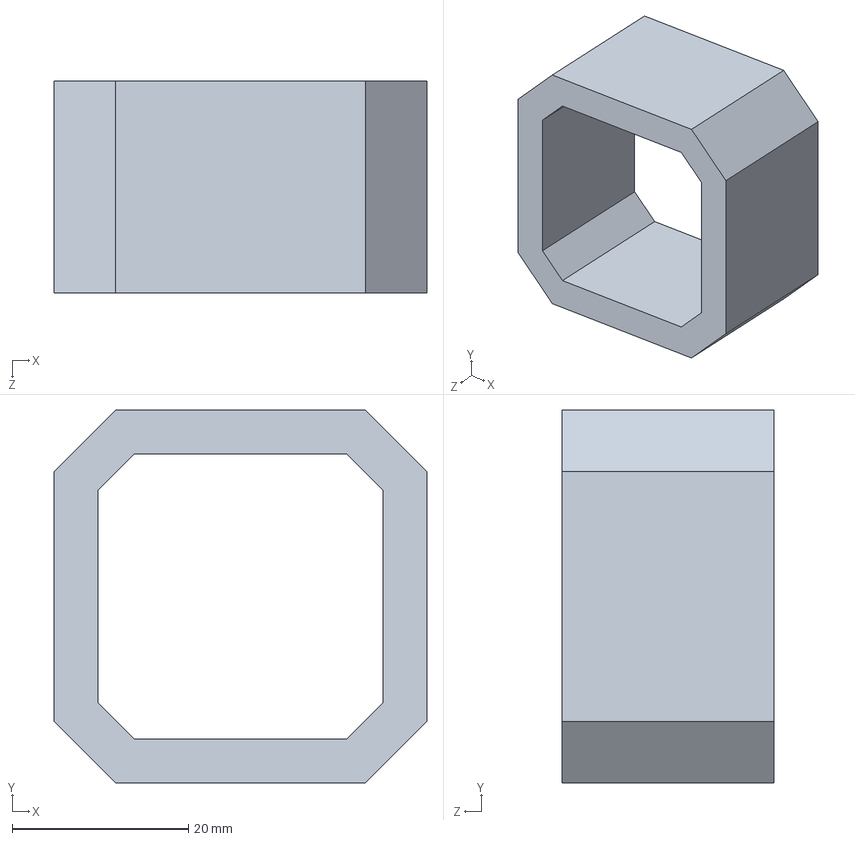
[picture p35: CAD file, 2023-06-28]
Allan/One axis drill project/Stepper motor/Body.SLDPRT
42.3 x 42.3 x 24.0 mm

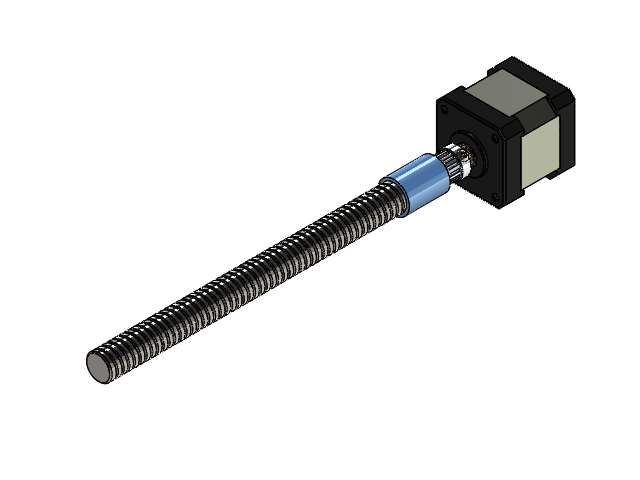
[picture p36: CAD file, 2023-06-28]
Allan/matlab/Stepper motor/sim assembley of stepper.SLDASM
case
rotary part

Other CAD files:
Allan/ansys/drill bit pmma.SLDASM
Allan/One axis drill project/Stepper motor/Assem1.SLDASM
Allan/One axis drill project/Dc motor/Assem1 dc motor.SLDASM
Allan/matlab/Stepper motor/case.SLDPRT
Allan/One axis drill project/Dc motor/Part2 motor.SLDPRT
Allan/One axis drill project/Dc motor/Part4 motor.SLDPRT
Allan/One axis drill project/Dc motor/Part5 motor.SLDPRT
Allan/One axis drill project/Dc motor/Part6 motor.SLDPRT
Allan/One axis drill project/Dc motor/coupler backup.SLDPRT
Allan/One axis drill project/Dc motor/dc motor.SLDPRT
Allan/One axis drill project/New drill bit.SLDPRT
Allan/One axis drill project/PMMA.SLDPRT
Allan/One axis drill project/Part2.1.SLDPRT
Allan/One axis drill project/Part2.SLDPRT
Allan/One axis drill project/Part4.SLDPRT
Allan/One axis drill project/Stepper motor/Base.SLDPRT
Allan/One axis drill project/Stepper motor/Pulley.SLDPRT
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

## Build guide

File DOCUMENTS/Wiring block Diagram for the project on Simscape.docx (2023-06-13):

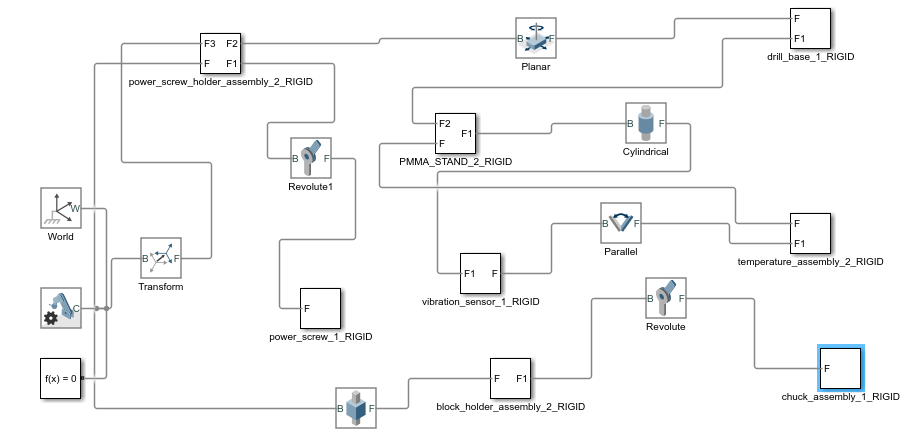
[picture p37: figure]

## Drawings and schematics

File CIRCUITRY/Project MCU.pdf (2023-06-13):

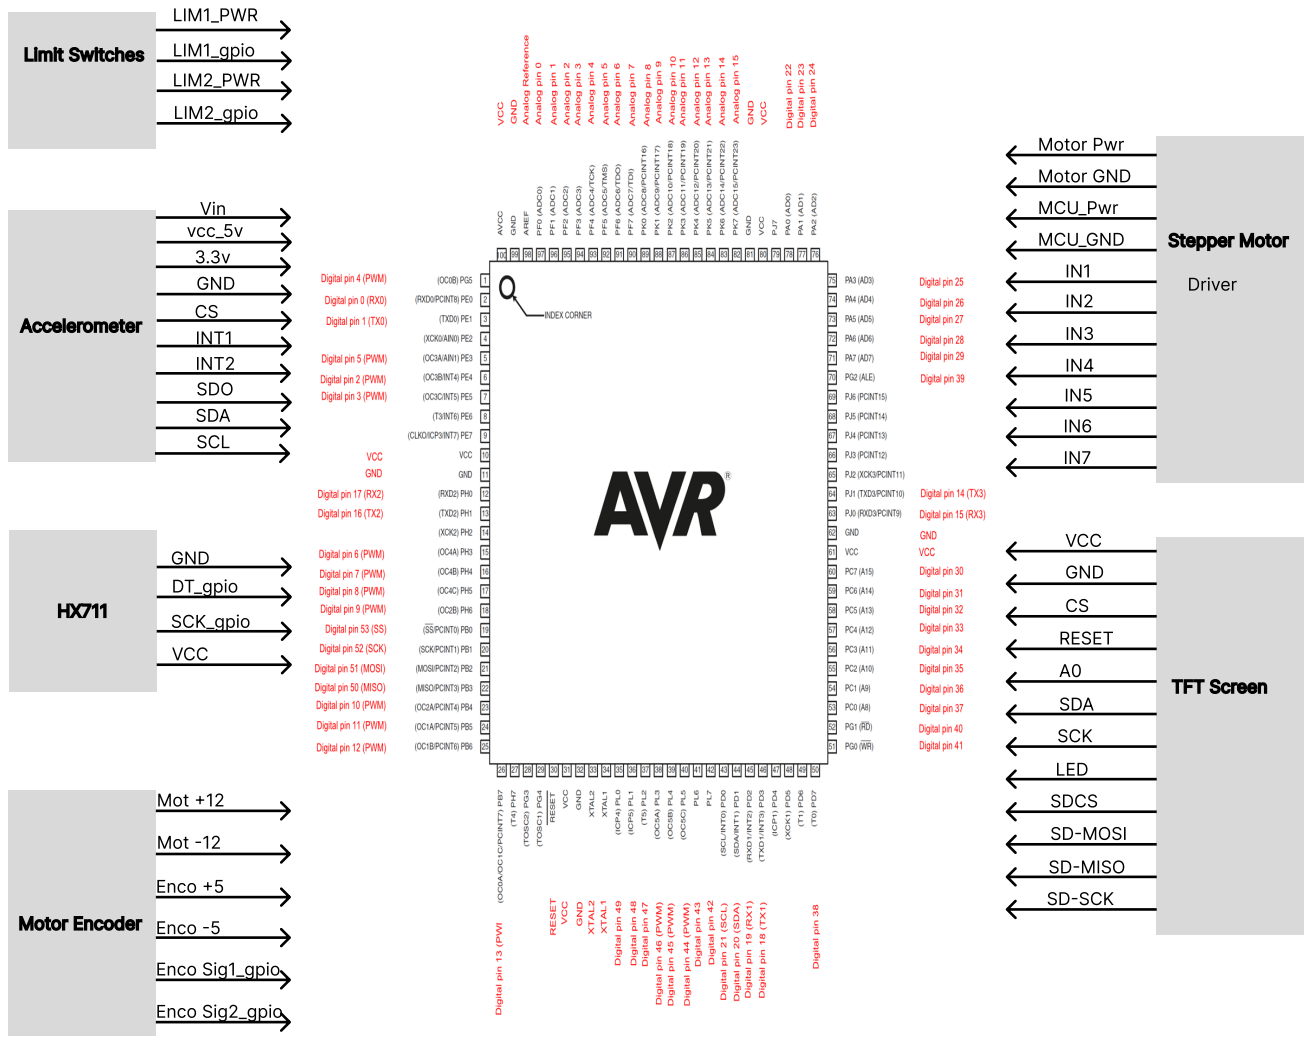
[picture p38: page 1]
TFT Screen; Motor Encoder; Accelerometer; Mot +12; Mot -12; Enco +5; Enco -5; Enco Sig1_gpio; Enco Sig2_gpio; Limit Switches; GND; DT_gpio; SCK_gpio; VCC; Vin; vcc_5v; INT1; INT2; SDO; SDA; SCL; Driver; Stepper Motor; LIM1_PWR; LIM1_gpio; LIM2_gpio; LIM2_PWR; Motor Pwr; Motor GND; MCU_Pwr; MCU_GND; RESET; SCK; LED; SDCS; SD-MOSI; SD-MISO; SD-SCK

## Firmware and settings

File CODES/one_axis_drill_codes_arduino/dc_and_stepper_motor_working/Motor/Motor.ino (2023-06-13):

//Define the DC motor connnection
int IN1 = 10;
int IN2 = 11;
int EN = 9;
int SPEED = 255;
int i;
int time = 3000;

// Limit Switch pin
int pin = 21;

// Define stepper motor connections and steps per revolution :
#define dirPin 50
#define stepPin 48
#define stepsPerRevolution 1600

void setup() 
{
  // Declare Stepper Motor pins as output:
  pinMode(stepPin, OUTPUT);
  pinMode(dirPin, OUTPUT);

  // Declare DC motor pins as output
  pinMode(IN1, OUTPUT);
  pinMode(IN2, OUTPUT);
  pinMode(EN, OUTPUT);

  //Interrupt function for the limit switch 
  attachInterrupt(digitalPinToInterrupt(21), Go_Home, CHANGE);
}

void Go_Home() {
  for (i=0; i<=100000; i++) {
    digitalWrite(dirPin, LOW);
    digitalWrite(stepPin, HIGH);
    delayMicroseconds(500);
    digitalWrite(stepPin, LOW);
    delayMicroseconds(500);
    if (digitalRead(20) == 1)
    {
      break;
    }
  }
}

void loop() 
{
  digitalWrite(dirPin,HIGH);
  digitalWrite(IN1, HIGH);
  digitalWrite(IN2, LOW);
  analogWrite(EN,255);
  digitalWrite(stepPin, HIGH);
  delayMicroseconds(20000);
  digitalWrite(stepPin, LOW);
  delayMicroseconds(20000);
}

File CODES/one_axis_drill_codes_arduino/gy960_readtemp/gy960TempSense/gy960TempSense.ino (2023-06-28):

#include <Adafruit_MLX90614.h>

Adafruit_MLX90614 mlx = Adafruit_MLX90614();

void setup() {
  Serial.begin(9600);
  while (!Serial);

  if (!mlx.begin()) {
    Serial.println("Error connecting to MLX sensor. Check wiring.");
    while (1);
  };
}

void loop() {
  Serial.print("Ambient temperature = "); 
  Serial.print(mlx.readAmbientTempC());
  Serial.print("°C");      
  Serial.print("   ");
  Serial.print("Object temperature = "); 
  Serial.print(mlx.readObjectTempC()); 
  Serial.println("°C");
  
  Serial.print("Ambient temperature = ");
  Serial.print(mlx.readAmbientTempF());
  Serial.print("°F");      
  Serial.print("   ");
  Serial.print("Object temperature = "); 
  Serial.print(mlx.readObjectTempF()); 
  Serial.println("°F");

  Serial.println("-----------------------------------------------------------------");
  delay(3000);
}
void readtemp(){
    Serial.print("Ambient temperature = "); 
  Serial.print(mlx.readAmbientTempC());
  Serial.print("°C");      
  Serial.print("   ");
  Serial.print("Object temperature = "); 
  Serial.print(mlx.readObjectTempC()); 
  Serial.println("°C");
}

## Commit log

2023-06-16 added simultaneous test with sensors
    added simultaneous test with sensors
2023-06-28 Design updates
    solid works parts and assembly design
    [Assem1 dc motor.SLDASM, Assem1.SLDASM, Axial Rod.SLDPRT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]
2023-06-28 improved update
    here we have matlab and ansys files for the project
    [Dc motor for simulink assembly 2.0.xml, New drill bit.IGS, case.SLDPRT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]
